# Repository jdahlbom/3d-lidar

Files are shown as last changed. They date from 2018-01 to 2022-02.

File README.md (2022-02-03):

3D lidar project
================

This is long work in progress project aiming to create a dome-like scanning lidar
implementation.

Current components are Garmin Lidar LITE v3 and Sparkfuns cheap pan-tilt brackets + servos.
Assuming I can produce useful distance point clouds with this setup, I might
next update the servo parts to something better. 

See [dev.log](./dev.log) for development notes.

Fritzing schematic of the device
--------------------------------
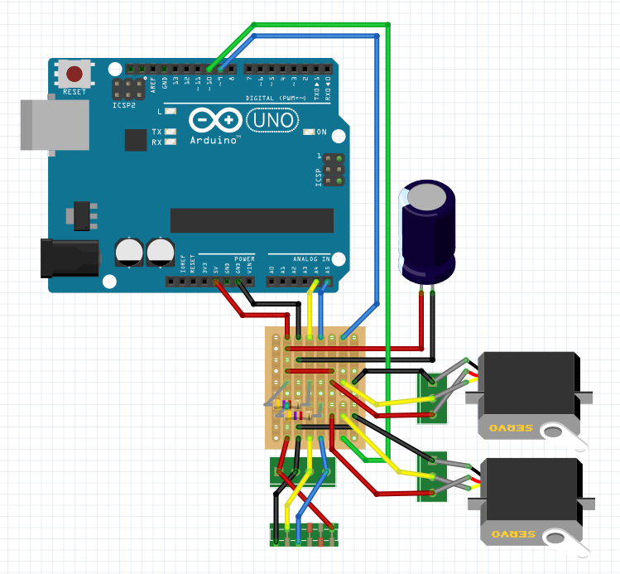
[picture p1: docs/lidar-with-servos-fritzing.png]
Servo + Lidars


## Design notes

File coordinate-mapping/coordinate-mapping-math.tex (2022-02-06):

\documentclass{article}

\usepackage[utf8]{inputenc}
\usepackage{pgfplots}
\usepackage{enumitem}
\usepackage{graphicx}
\usepackage{amsmath}

\begin{document}
\title{Coordinate mapping for pan/tilt Lidar}
\author{Jukka Dahlbom}
\maketitle

Conversion from polar coordinates and lidar servo structure
to cartesian coordinates is done with translation/rotation matrix
multiplication.
    
\section*{The structure}
These are the structure conversions, using positive x as "forward", y as "right" and z as "upwards" axies - a "left handed" axis setup,
and starting with measurements lidar distance $d$, pan angle $\alpha$ and tilt angle $\beta$:
\begin{itemize}
\item Rotation arm attach point is the origin.
\item The pan servo and attachment arm gives us rotation alpha around $z$-axis
\item The tilt servo rotates the device by $\beta$ around 
the $y$-axis.
\item Distance from Lidar is the measurement position relative to Lidar $X = \begin{bmatrix}d & 0 & 0 & 1 \end{bmatrix}^T$
\end{itemize}

Pan rotation matrix:

\begin{equation}
M_{pan} =
\begin{bmatrix}
  cos(\alpha) & -sin(\alpha) &	0	& 0\\
  sin(\alpha) &	cos(\alpha)	 &  0   & 0\\
  0			  & 0			 &	1	& 0\\
  0			  &	0			 &	0	& 1
\end{bmatrix}
\end{equation}

Tilt rotation matrix:

\begin{equation}
M_{tilt} =
\begin{bmatrix}
  cos(\beta)  & 0		     &	-sin(\beta)	& 0\\
  0			  &	1			 &  0   & 0\\
  sin(\beta)  & 0			 &	cos(\beta)	& 0\\
  0			  &	0			 &	0	& 1
\end{bmatrix}
\end{equation}

Due to bracket attachments, there is also \emph{translation} 
terms in addition to rotation. 
In the early stages we could assume they 
are zero, or significantly less than measured distances and 
therefore irrelevant.

The transformation matrices above look like this with translation
terms:

Pan transformation matrix:

\begin{equation}
M_{pan} =
\begin{bmatrix}
  cos(\alpha) & -sin(\alpha) &	0	& p_x\\
  sin(\alpha) &	cos(\alpha)	 &  0   & p_y\\
  0			  & 0			 &	1	& p_z\\
  0			  &	0			 &	0	& 1
\end{bmatrix}
\end{equation}

Tilt transformation matrix:
\begin{equation}
M_{tilt-t} =
\begin{bmatrix}
  cos(\beta)  & 0		     &	-sin(\beta)	& t_x\\
  0			  &	1			 &  0   		& t_y \\
  sin(\beta)  & 0			 &	cos(\beta)	& t_z \\
  0			  &	0			 &	0	& 1
\end{bmatrix}
\end{equation}

In my arrangement, $d_y$ term is zero in both cases - there is no sideways translation.

The applied transformation is in entirety:

\begin{equation}
X' = M_{pan} * M_{tilt} * X
\end{equation}

Without translation terms:
\begin{equation}
X' =
\begin{bmatrix}
cos(\alpha)*cos(\beta)	& -sin(\alpha) & cos(\alpha)*-sin(\beta) & 0\\
sin(\alpha)*cos(\beta) 	& cos(\alpha) & sin(\alpha)*-sin(\beta) & 0\\
sin(\beta)	&	0 & cos(\beta)	&	0\\
0 & 0 & 0 & 1
\end{bmatrix}
*
\begin{bmatrix}
d \\ 0 \\ 0 \\ 1
\end{bmatrix}
\end{equation}

\begin{equation}
X' = 
\begin{bmatrix}
d_x' \\
d_y' \\
d_z' \\
1
\end{bmatrix}
=
\begin{bmatrix}
d * cos(\alpha) * cos(\beta) \\
d * sin(\alpha) * cos(\beta) \\
d * sin(\beta) \\
1
\end{bmatrix}
\end{equation}

With translation terms (remember that $t_y = p_y = 0$) the combined translation matrix is:
\begin{equation}
X' = 
\begin{bmatrix}
cos(\alpha)*cos(\beta) & -sin(\alpha) & cos(\alpha)*-sin(\beta) & cos(\alpha)*t_x + p_x \\
sin(\alpha)*cos(\beta) & cos(\alpha) & sin(\alpha)*cos(\beta) &
sin(\alpha)*t_x + p_y \\
sin(\beta)	&	0	& cos(\beta) & t_z + p_z \\
0 & 0 & 0 & 1
\end{bmatrix}
* X
\end{equation}

Transformed coordinates are in this case:
\begin{equation}
X' = 
\begin{bmatrix}
d * cos(\alpha) * cos(\beta) + cos(\alpha)*t_x + p_x \\
d * sin(\alpha) * cos(\beta) + sin(\alpha)*t_x \\
d * sin(\beta) + t_z + p_z \\
1
\end{bmatrix}
\end{equation}

\section*{Problems and questions}
In order to produce numbers relative to origin, translation
values in both pan and tilt matrices should be substracted
from the result instead of adding them.

This is most easily solved by making the $t_x$, $p_x$, $t_z$ and
$p_z$ values negative. It bothers me though, this needs
to be drawn out to properly figure out the conceptual change.

\end{document}

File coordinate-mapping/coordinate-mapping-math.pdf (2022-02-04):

# Coordinate mapping for pan/tilt Lidar

Jukka Dahlbom

February 4, 2022

Conversion from polar coordinates and lidar servo structure to cartesian coordinates is done with translation/rotation matrix multiplication.
These are the structure conversions, using positive x as ”forward”, y as ”right” and z as ”upwards” axies - a ”left handed” axis setup, and starting with measurements lidar distance d, pan angle α and tilt angle β:
| Rotation arm attach point is the origin.
| The pan servo and attachment arm gives us rotation alpha around z-axis
| The tilt servo rotates the device by β around the y-axis.
| Distance from Lidar is the measurement position relative to Lidar X = - d 0 0 1T

Pan rotation matrix:

Mpan =

cos(α) −sin(α) 0 0
sin(α) | cos(α) | 0 0
0 | 0 | 1 0
0 | 0 | 0 1

(1)

Tilt rotation matrix:

Mtilt =

cos(β) 0 −sin(β) 0
0 | 1 | 0 | 0
sin(β) 0 | cos(β) | 0
0 | 0 | 0 | 1

(2)

Due to bracket attachments, there is also translation terms in addition to rotation. In the early stages we could assume they are zero, or significantly less than measured distances and therefore irrelevant.
The transformation matrices above look like this with translation terms: Pan transformation matrix:

Mpan =

cos(α) −sin(α) 0 px
sin(α) | cos(α) | 0 py
0 | 0 | 1 pz
0 | 0 | 0 | 1

(3)

1

Tilt transformation matrix:

Mtilt−t =

cos(β) 0 −sin(β) tx
0 | 1 | 0 | ty
sin(β) 0 | cos(β) | tz
0 | 0 | 0 | 1

(4)

In my arrangement, dy term is zero in both cases - there is no sideways translation.
The applied transformation is in entirety:
X⁰ = Mpan ∗ Mtilt ∗ X | (5)

Without translation terms:

X⁰ =

cos(α) ∗ cos(β) −sin(α) cos(α) ∗ −sin(β) 0
sin(α) ∗ cos(β) | cos(α) | sin(α) ∗ −sin(β) 0
sin(β) | 0 | cos(β) | 0
0 | 0 | 0 | 1

∗

d
0
0
1

(6)

X⁰ =

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
d ∗ cos(α) ∗ cos(β)
d ∗ sin(α) ∗ cos(β)
d ∗ sin(β)
1

(7)

With translation terms (remember that ty = py = 0) the combined translation matrix is:

X⁰ =

cos(α) ∗ cos(β) −sin(α) cos(α) ∗ −sin(β) cos(α) ∗ tx + px
sin(α) ∗ cos(β) | cos(α) | sin(α) ∗ cos(β) | sin(α) ∗ tx + py
sin(β) | 0 | cos(β) | tz + pz
0 | 0 | 0 | 1

∗ X

(8)
Transformed coordinates are in this case:

X⁰ =

d ∗ cos(α) ∗ cos(β) + cos(α) ∗ tx + px d ∗ sin(α) ∗ cos(β) + sin(α) ∗ tx d ∗ sin(β) + tz + pz
1

(9)

2

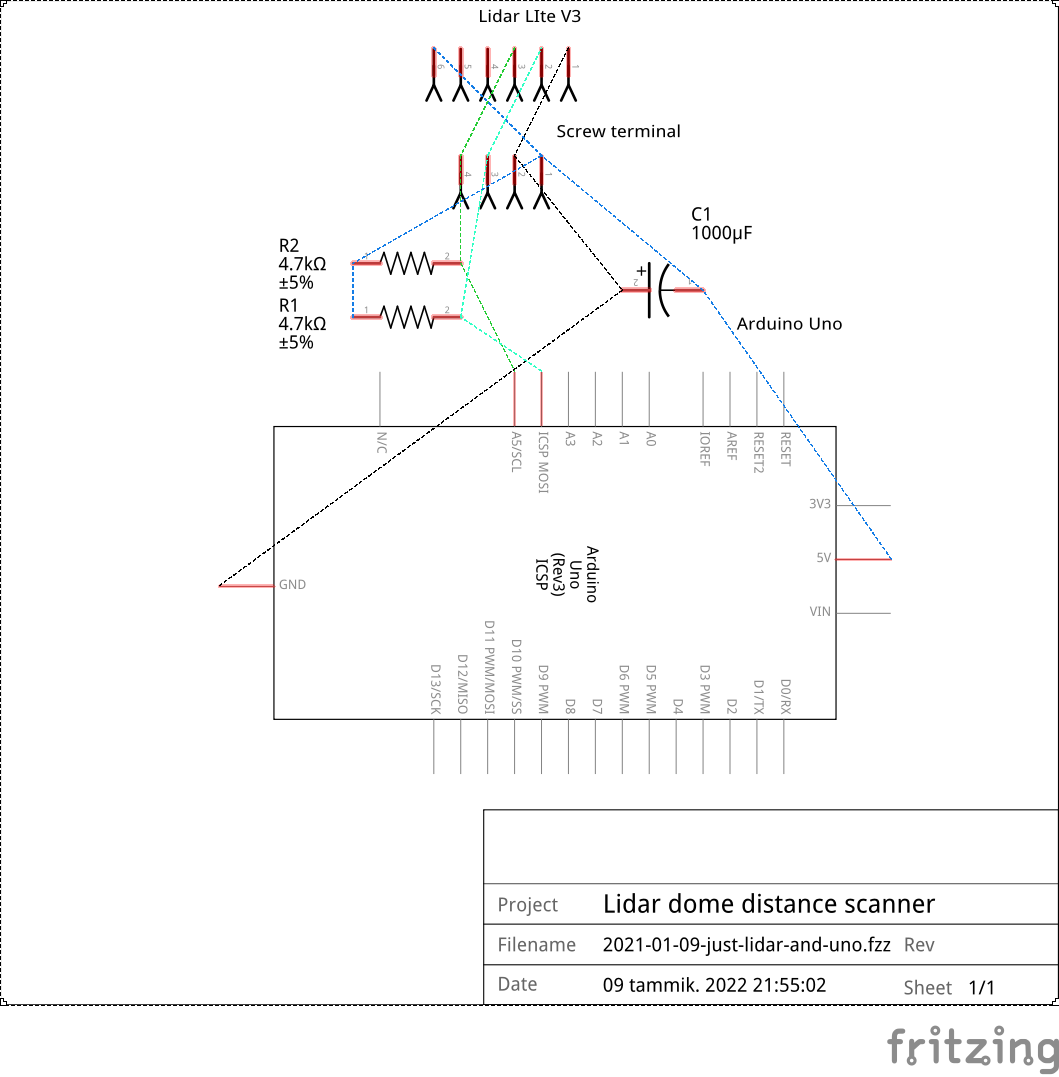
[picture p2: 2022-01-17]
cad/2021-01-09-just-lidar-and-uno_schem.png

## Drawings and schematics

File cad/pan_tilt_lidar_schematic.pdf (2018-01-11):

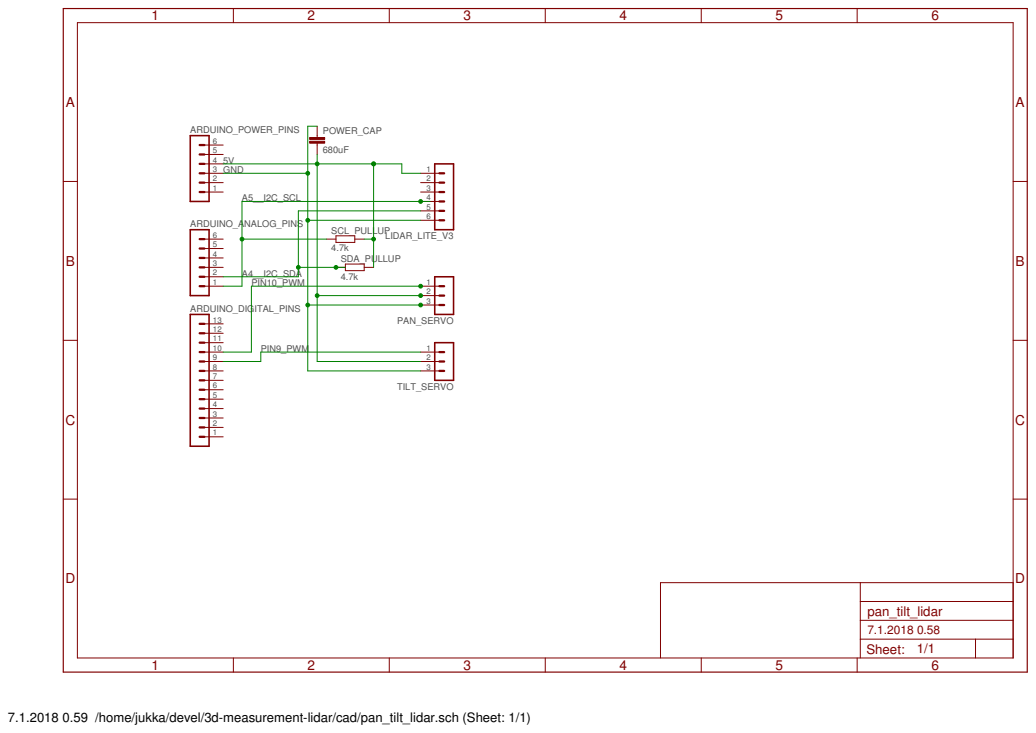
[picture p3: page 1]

7.1.2018 0.59 /home/jukka/devel/3d-measurement-lidar/cad/pan_tilt_lidar.sch (Sheet: 1/1)

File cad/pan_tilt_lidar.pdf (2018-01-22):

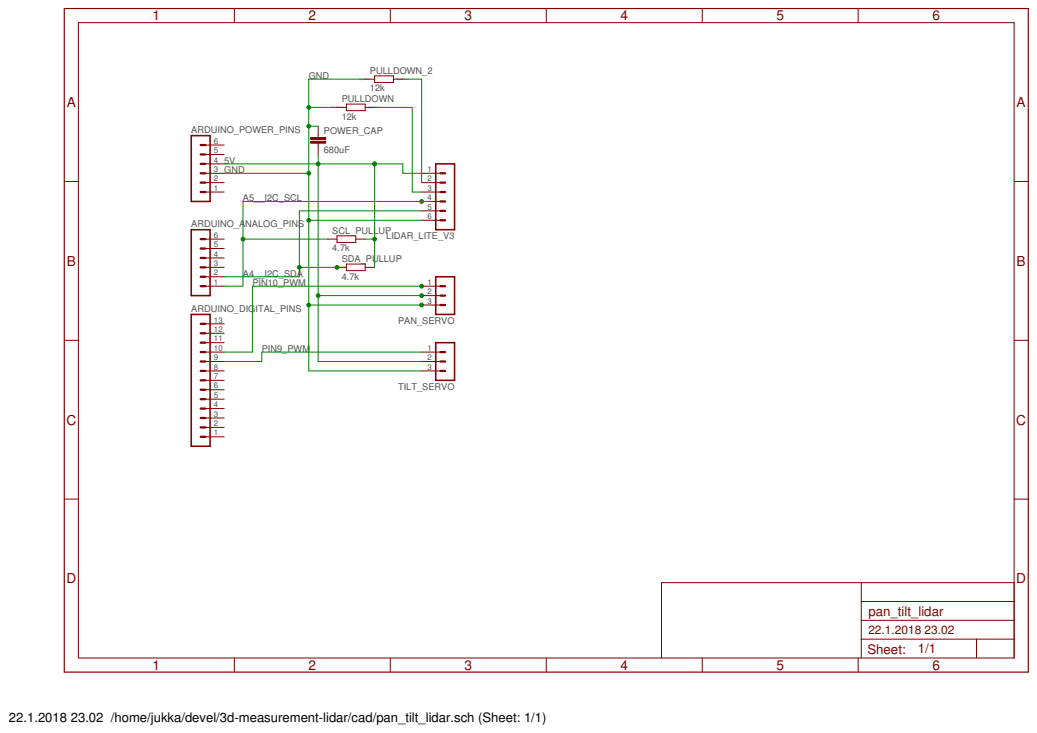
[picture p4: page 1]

22.1.2018 23.02 /home/jukka/devel/3d-measurement-lidar/cad/pan_tilt_lidar.sch (Sheet: 1/1)

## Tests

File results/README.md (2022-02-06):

Coordinate mapping from serial output file
==========================================

- Store the serial output as "raw-YYYY-mm-dd-hhMM.csv"
- Grep for "^<jobID>," where jobId is the id you gave the scan result set.
- Save as "YYYY-mm-dd-hhMM.csv"  ( `grep "^<jobID>," raw-YYYY-mm-dd-hhMMcsv YYYY-mm-dd-hhMM.csv` )
- run "python3 coord-mapping.py YYYY-mm-dd-hhMM.csv > cartesian-YYYY-mm-dd-hhMM.csv"
- TODO: Convert the cartesian csv data into LAS file format for viewing

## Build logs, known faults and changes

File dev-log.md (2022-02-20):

Development log
===============

Monday, Jan 22nd, 2018
----------------------
Picked up from where I left a week ago:
- Servo control is working, but the pan servo is aligned off to the side.
- Attachment plate for the lidar<->servo connection needs to be designed,
  it's more trouble than worth to rig something temporary compared to ordering 3d printed plate.
- Lidar measurements & I2C is untested, circuit schematic created for the wiring.

Decided to focus solely on the Lidar measurements and I2C aspect.
I begun by grounding the unused PWM-pins in the Lidar wiring just in case. I used 12 kohm resistors between the pin and GND.
Could not get any reading from the Lidar - not sure if the measurement should be visible laser but if so, the whole
measurement is not working at all. Tried using the I2C for reading, but didn't really measure I2C properly for it.

I'm still missing the recommended 680uF capacitor between 5V and GND, will have to scrounge older projects for the capacitor.

/ Jukka

Monday, Jan 29th, 2018
----------------------
We're using DSSCircuits.com Arduino I2C Master Library in order to use multibyte read support available in Lidar Lite v3
dsscircuits.com/articles/86-articles/66-arduino-i2c-master-library

Earlier code didn't send the mearurement byte.

Useful example of I2C was found at https://github.com/PulsedLight3D/LIDARLite_StateMachine

Rewrote the read logic to similar to PulsedLight3D example.
Got huge 680uF 200V capacitors to wait for installation.

Next up: Set up the capacitor, test the new I2C code. I expect it's still not working at first try.
If there are problems, one more potential reason might be the pullup resistor setup which is
a "best guess" at the moment.

/ Jukka

Saturday, Dec 25, 2021
----------------------
Reviving old project: Last recollection was that I never got the I2C working back in 2018.

Got possibly better hookup guide: https://learn.sparkfun.com/tutorials/lidar-lite-v3-hookup-guide

Guide mentions that I2C devices are very sensitive to connection failures, and recommends
soldering wires instead of relying on just a breadboard.
This is probably why I ordered protoboards back when I was last working on the project.

Monday, Jan 17, 2022
--------------------
I got the LIDAR part done with stripboard. The hookup guide above mentioned that
I2C is very sensitive to contact errors, so I soldered everything together with the stripboard
and soldered the I2C wires to male pin headers which connect to Arduino.
Worked with first attempt.

Next part is adding the pan-tilt servo control.
Looks like the easiest approach to that is using Arduino Servo-library.
https://github.com/arduino-libraries/Servo/blob/master/src/Servo.h

Found useful example code here:
https://maker.pro/arduino/tutorial/how-to-set-up-pan-tilt-camera-stand-with-arduino-uno-and-joystick-module

Someone somewhere also mentioned that the servo controls seems wrong,
and the servo doesn't actually turn as much as it should. They had fixed it
by using shorter PWM cycle length. Look into it if servos are not working well.

Sunday, Jan 30, 2022
--------------------

Theory notes:
- Easy way of logging the arduino output might be with screen:
  https://www.pragmaticlinux.com/2021/11/how-to-monitor-the-serial-port-in-linux/

- I should add a reset switch to the project - something that leads to servos resetting to
  their initial position, generating a new run id for the scan and starting the scan anew.

- In order to map the scanner outputs values (tilt, pan, distance) I will need to 
  compute the conversion matrces - for example: 
  https://www.brainvoyager.com/bv/doc/UsersGuide/CoordsAndTransforms/SpatialTransformationMatrices.html

Sunday, Feb 06, 2022
--------------------

Math part finally nearing potential usefulness. There are several conversions to note
which are detailed in the LaTeX document.
Current implementation gives correct height value within the +-2.5cm measurement error range
when measuring from the floor to device origin.

Results are stored as CSV for intermediate use.

There is a lidar data visualizer site which I intend to make use of for validating the lidar data
conversions and usage - as far as I need to for current measurements: 
http://lidarview.com/

Lidarview uses LAS 1.2 formatted input files, so next part is converting cartesian xyz-coordinate CSV into
LAS 1.2 file. Automating this pipeline improves my feedback time from device measurements to 
visually inspectable image that can be improved. Same goes for combining possible future measurements from several 
device locations in the same scene / 3d space.

Sunday, Feb 13, 2022
--------------------

Added intensity measurement. Noticed that my matte hanged images show difference in lidar intensity depending
on the viewing angle: From straight ahead it does not differ from matte wall, from more 
acute angle it shows significant difference.

Updated the pan/tilt angle step to 1 degree, and was happy to notice that even current wobbly construction
of lidar arm gives fairly proper results.

Open issue: Serial printing in different rows seems to occasionally skip some characters. This might
have to do with printing several entries in sequence, rather than printing it all in one printf

Sunday, Feb 20, 2022
--------------------

Was able to run the scan with 1 degree differences. Realized that in order to build a proper scene,
I need to patch together a set of different angles from same origin pointi. Instead of patching several
measurement sets together, I'd much rather build a better mounting for the lidar that allows free 360 degree
panning.
Ideally one that would get rid of the vibration and wobbliness issues. It would be possible to also set
up the lidar so that the lidar itself woulbe in the origin point of the measurements, even without translating
the angular measurements by the lidar control arm dimensions. With proper wiring we should be able to get
rid of the current situation where lidar has to drag its wiring at more extreme angles.

So next part is learning about motors or continuous rotation servos. In order to deliver power and signals
to freely panning system, we need to have a slip ring. Promising cheap option for it is the 2A 12 wire Sparkfun slip ring
https://www.sparkfun.com/products/13065

For now, I will see if I could build the lidar mount system using some readily available build kits such
as the Actobotics product line: https://www.sparkfun.com/videos#actobotics/d3MBTT10pxk

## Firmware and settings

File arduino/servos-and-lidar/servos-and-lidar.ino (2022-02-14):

#include <Servo.h>
#include <Wire.h>
#include <LIDARLite.h>

const int servoPinPan = 9;       // first servo
const int servoPinTilt = 10;     // second servo

Servo panServo;  // create servo object to control a servo
Servo tiltServo;  // create servo object to control a servo

const int maxPan = 150;
const int minPan = 30;
const int maxTilt = 120;
const int initialTiltCorrection = 30;
int panIncrement = 1;
int tiltIncrement = 1;
const int stopDelay = 100;
const int lidarDelay = 10;

int loopCount = 0;
int pan;
int tilt;
int runId;
bool blockLooping = true;

LIDARLite lidarLite;
void setup()
{
  Serial.begin(9600); // Initialize serial connection to display distance readings

  lidarLite.begin(0, true); // Set configuration to default and I2C to 400 kHz
  lidarLite.configure(0); // Change this number to try out alternate configurations

  // Servo  
  panServo.attach(servoPinPan);  // attaches the servo
  tiltServo.attach(servoPinTilt);  // attaches the servo

}

/**
 * Prompt for scan set identifier
 * Returns integer value to use as result set ID.
 */
int prompt() {
  resetInitialValues();
  Serial.println("#==========================#");
  Serial.println("#  Pan-tilt Lidar scanner  #");
  Serial.println("#  Scan prompt             #");
  Serial.println("#==========================#");
  Serial.println("#");
  while(true) {
    Serial.println("#> Send integer value to use as scan result identifier");
    while(!Serial.available()) {
      delay(5);
    }
    int input = Serial.parseInt();
    if (input != 0) {
      Serial.print("# Starting scan run ");
      Serial.println(input);
      Serial.println("# CSV header:");
      Serial.println("runId,distance,pan,tilt");
      blockLooping = false;
      return input;
    } else {
      Serial.print("#! Invalid input, please input integer value");
    }
  }
}

void sendScanResults(int runId, int distance, int intensity, int pan, int tilt) {
  Serial.print(runId);
  Serial.print(",");
  Serial.print(distance);
  Serial.print(",");
  Serial.print(intensity);
  Serial.print(",");
  Serial.print(pan);
  Serial.print(",");
  Serial.println(tilt);
}

void resetInitialValues() {
  pan = minPan;
  tilt = 0;

  tiltServo.write(tilt);
  panServo.write(pan);
  delay(2000);
}

/**
 * Servo bracket right now uses "0" tilt as maximum upwards tilt it goes to.
 * It is in reality somewhere around 60 tilt from horizontal plane (90 - initialTiltCorrection)
 */
int mapServoTiltToRealTilt(int tilt) {
  return 90 - tilt - initialTiltCorrection;
}

/**
 * Pan servo is at middle initial position when given value "90". Middle position should be
 * 0 pan.
 */
int mapServoPanToForwardZeroPan(int pan) {
  return pan - 90;
}

int lidarIntensity() {
  byte isBusy = 1;
  // Poll busy bit in status register until device is idle
  while(isBusy)
  {
  // Read status register
    Wire.beginTransmission(LIDARLITE_ADDR_DEFAULT);
    Wire.write(0x01);
    Wire.endTransmission();
    Wire.requestFrom(LIDARLITE_ADDR_DEFAULT, 1);
    int statusByte = Wire.read();
    isBusy = bitRead(statusByte,0); // Take LSB of status register, busy bit
  }
  // read register 0x0e which is signal strength
  Wire.beginTransmission(LIDARLITE_ADDR_DEFAULT);
  Wire.write(0x0e);
  Wire.endTransmission();
  Wire.requestFrom(LIDARLITE_ADDR_DEFAULT, 1);
  return Wire.read();
}

void loop(){
    if (blockLooping == true) {
      runId = prompt();
    }
    else {
      pan += panIncrement;
      if (pan > maxPan) {
        pan = maxPan;
        panIncrement = 0-panIncrement;
        tilt += tiltIncrement;
      }
      if (pan < minPan) {
        pan = minPan;
        panIncrement = 0-panIncrement;
        tilt += tiltIncrement;        
      }
      if (tilt >= (maxTilt-initialTiltCorrection) && pan == maxPan) {
        blockLooping = true;
        return;
      }
    }
    
    tiltServo.write(tilt);
    panServo.write(pan);
    delay(stopDelay);
    int dist;
    if (loopCount == 100) {
      dist = lidarLite.distance();
      loopCount = 0;
    } else {
      dist = lidarLite.distance(false);
      loopCount++;
    }
    int intensity = lidarIntensity();
    delay(lidarDelay);
    sendScanResults(runId, dist, intensity, mapServoPanToForwardZeroPan(pan), mapServoTiltToRealTilt(tilt));
}

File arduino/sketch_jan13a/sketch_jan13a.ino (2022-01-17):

/**
* LIDARLite I2C Example
* Author: Garmin
* Modified by: Shawn Hymel (SparkFun Electronics)
* Date: June 29, 2017
*
* Read distance from LIDAR-Lite v3 over I2C
*
* See the Operation Manual for wiring diagrams and more information:
* http://static.garmin.com/pumac/LIDAR_Lite_v3_Operation_Manual_and_Technical_Sp
ecifications.pdf
*/
#include <Wire.h>
#include <LIDARLite.h>
// Globals
LIDARLite lidarLite;
int cal_cnt = 0;
void setup()
{
  Serial.begin(9600); // Initialize serial connection to display distance readings
  lidarLite.begin(0, true); // Set configuration to default and I2C to 400 kHz
  lidarLite.configure(0); // Change this number to try out alternate configurations
}

void loop() {
  int dist;
  // At the beginning of every 100 readings,
  // take a measurement with receiver bias correction
  if ( cal_cnt == 0 ) {
  dist = lidarLite.distance();
  // With bias correction
  } else {
  dist = lidarLite.distance(false); // Without bias correction
  }

  // Increment reading counter
  cal_cnt++;
  cal_cnt = cal_cnt % 100;
  // Display distance
  Serial.print(dist);
  Serial.println(" cm");
  delay(10);
}

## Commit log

2018-01-11 Initial data, datasheets and schematics
    [arduino_Uno_ref.brd, arduino_Uno_ref.sch, pan_tilt_lidar.sch]
2018-01-22 [lidar] Testing lidar readings
2018-01-22 [cad & i2c] Figuring out I2C issues
    [pan_tilt_lidar.sch]
2018-01-29 Lidar code fix
2022-01-17 Lidar sketch & code, is working
    [2021-01-09-just-lidar-and-uno.fzz]
2022-02-03 Servo + lidar schematic
    [2022-02-03-lidar-uno-and-servos.fzz]
2022-02-03 Arduino servo code
2022-02-06 Cartesian mapping from polar coordinate results
    [2022-02-06-2105.csv, cartesian-2022-02-06-2105.csv, raw-2022-02-06-2105.csv]
2022-02-06 LAS files generation from cartesian coords
    [2022-02-06-2105-cartesian.csv]
